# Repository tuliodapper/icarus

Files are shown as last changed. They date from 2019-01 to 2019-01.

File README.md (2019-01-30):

# icarus
This project consists of designing, building and testing a mobile robot. The system is a self-contained robot able to negotiate a maze in the shortest possible time. In the micromouse project rules, the maze is composed by 16x16 squares; the goal (2x2 square) is placed in the centre of the maze. Starting from a corner of the maze, the micromouse needs to complete the maze without any external help. For completing the maze, firstly, the micromouse needs to find the centre. After that, the robot needs to return to the start position and then execute the fast route to the centre. The work involves a huge number of skills that is included in a mobile robot, such as working with embedded programming, designing and building PCB boards, dealing with sensor components and solving mechanical issues.

## Folders

### doc
Contains report, presentation and video.

### software
Contains MATLAB code for the control panel interface, which aims to monitor sensor values and set robot parameters. Use MATLAB R2015a or later versions.

### firmware
Contains C code for the firmware of the mobile robot.

### hardware
Contains the board EAGLE files for the hardware of the mobile robot.

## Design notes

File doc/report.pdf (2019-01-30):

Bristol, 24 May 2015

UFMFKA-30-2 – GROUP FAB LAB FINAL GROUP REPORT

# Group Fab Lab

# Final Group Report

Authors:

Ícaro Almeida (14004456)

Leonardo Jurado (10023227)

Sanyog Chhetri (13021702)

Túlio Dapper e Silva (14004454)

## Contents

## Section 1

### Introduction

The micromouse project consists of designing, building and testing a mobile robot. The

system is a self-contained robot able to negotiate a maze in the shortest possible time. In the

micromouse project rules, the maze is composed by 16x16 squares; the goal (2x2 square) is

placed in the centre of the maze. Starting from a corner of the maze, the micromouse needs

to complete the maze without any external help. For completing the maze, firstly, the

micromouse needs to find the centre. After that, the robot needs to return to the start position

and then execute the fast route to the centre.

The work involves a huge number of skills that is included in a mobile robot. The group

needs to work with programming for embedded systems, design and build of PCB boards,

deal with sensor components and solve mechanical issues. This document includes a brief

explanation about how the software and hardware were built and how the group has been

distributed tasks; in addition, it also includes the problems encountered and most suitable

approaches.

### Conceptual Design

The micromouse was designed in a modular approach. As a consequence, boards

could be more easily tested, modified and hardware issues could be solved separately. In

addition, a sensor board for testing could be built before designing and building the other

boards, which enabled the use of the Firecracker as the initial testing platform. At the end, as

the system was modular and the group faced an unexpected problem with the final sensor

board, the testing sensor board was still being used.

Four different boards were designed and built: power supply board, main board

(containing the microcontrollers), sensor board and motor board. In order to separate the

boards inside the micromouse, mechanical spacers were used. In total, the micromouse

ended up with 3 floors. In the first floor, the micromouse has two boards: the sensor board and

the motor board. The sensor board was placed on front of the motors for taking readings. The

motor board was place in the back of the motors. The main board is located in the second

floor; the last floor is used for the supply board.

On the supply board, a linear low dropout regulator was used with an appropriate heat

sink; reverse-polarity protection diodes and appropriate capacitors (as on the datasheet) were

also used. Two buttons and four LEDs were also placed on this board.

In order to store the programs into the microcontrollers, the group opted to design an

external board that can be attached to the main board via an Ethernet cable. On the external

board, there are switches to toggle between PIC 1 and 2. In both PICs, the PGC and PGD

pins were exclusively used for the burning process, avoiding switches; therefore it was

necessary to use the alternative UART ports.

On the motor driver board, the IC L293DNE was used as it supports the current drained

by the motors and also has diodes built-in. The only protective components attached outside

were the decoupling capacitors recommended on the datasheet and a unidirectional TVS as

it is faster than the bidirectional ones. A TVS is basically a diode with a lower breakdown

voltage, so it was used in addition to the internal diodes to protect the circuit from over voltages

generated by the motor coils as a consequence of the back-EMF.

On the sensor board, transistors were used to switch each IR LED due to the high

current they drain, which is nearly a hundred milliamps each.

### Project Planning

The group is composed of four members. In order to execute the micromouse work,

different tasks were assigned for each member. As a consequence, each member was

responsible for searching, developing, presenting and documenting their own part of the

project. During these stages, the other members were completely willing to help. The division

of the tasks were made as shown in Figure 1.

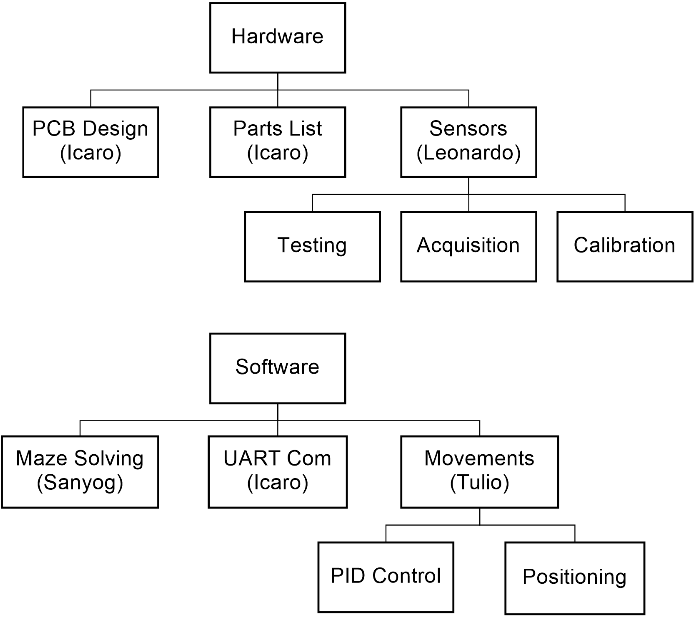
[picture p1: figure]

Figure 1: Division of the tasks between members.

As the project had deadlines to be respected, tasks should be executed within certain

period of time. In order to guarantee enough time for all tasks, a Gantt chart were built. The

first chart built is depicted in Figure 2. As can be seen in the figure, software structure (creating

headers with main constants and functions) and parts list should have be done by the end of

December. In addition, all the embedded programming should be finished by the middle of

January. The decision was based on having a long time for “Testing and Improvements”, which

should have two months of work. However, the work was not executed as planned.

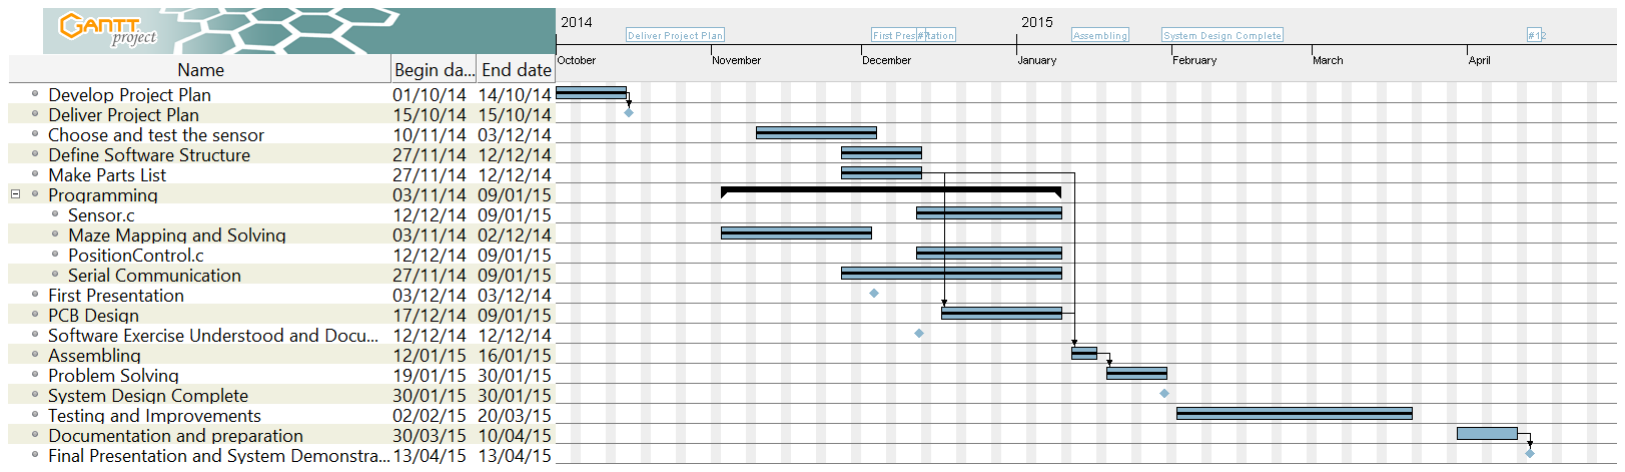
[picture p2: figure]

Figure 2: Gantt chart before executing the project.

At the end, the amount of time spent for each task is depicted in Figure 3. As can be

seen, some tasks took longer than expected. The main reason for those delays is that the

assigned duration for some tasks were not enough for the work load. The group were not

expecting to have problems that came from the lack of experience of the members. In addition,

most of the components were being frequently changed during the process. As a

consequence, the parts list was not completed in time; without the components, assembling

and testing were also being procrastinated. As a micromouse prototype was being used for

testing, the group was waiting as much as possible in order to design and build the final

version.

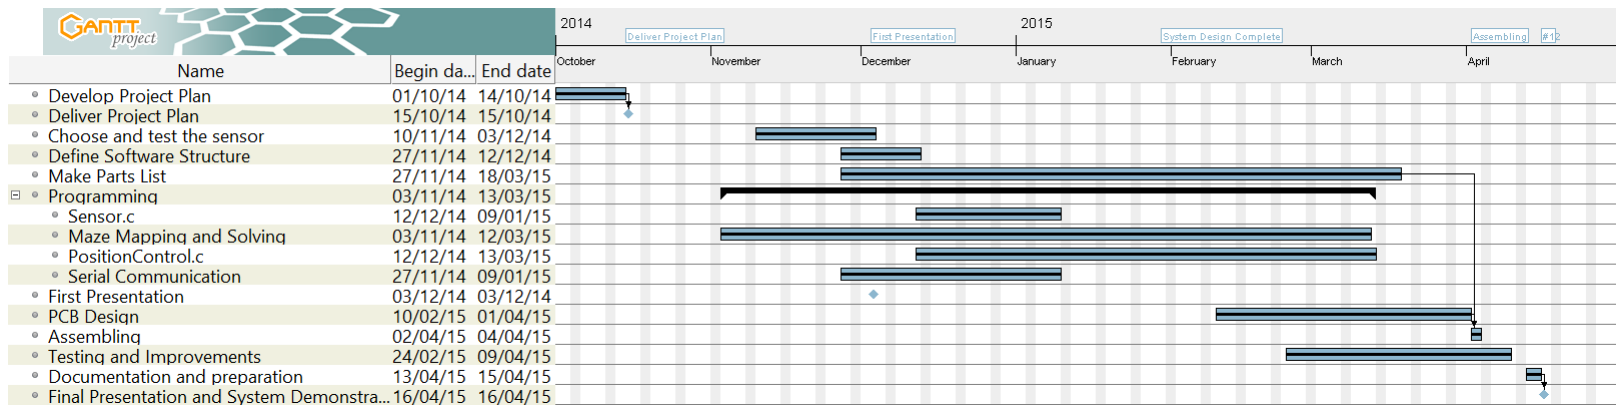
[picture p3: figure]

Figure 3: Gantt chart after executing the project.

### Controller Design

The software were designed in order to facilitate that each member could develop a

part separately. For that reason, meetings were needed in order to create headers and set up

how methods were interacting each other. The Figure 4 depicts, using UML class diagrams,

how main headers were designed and related each other.

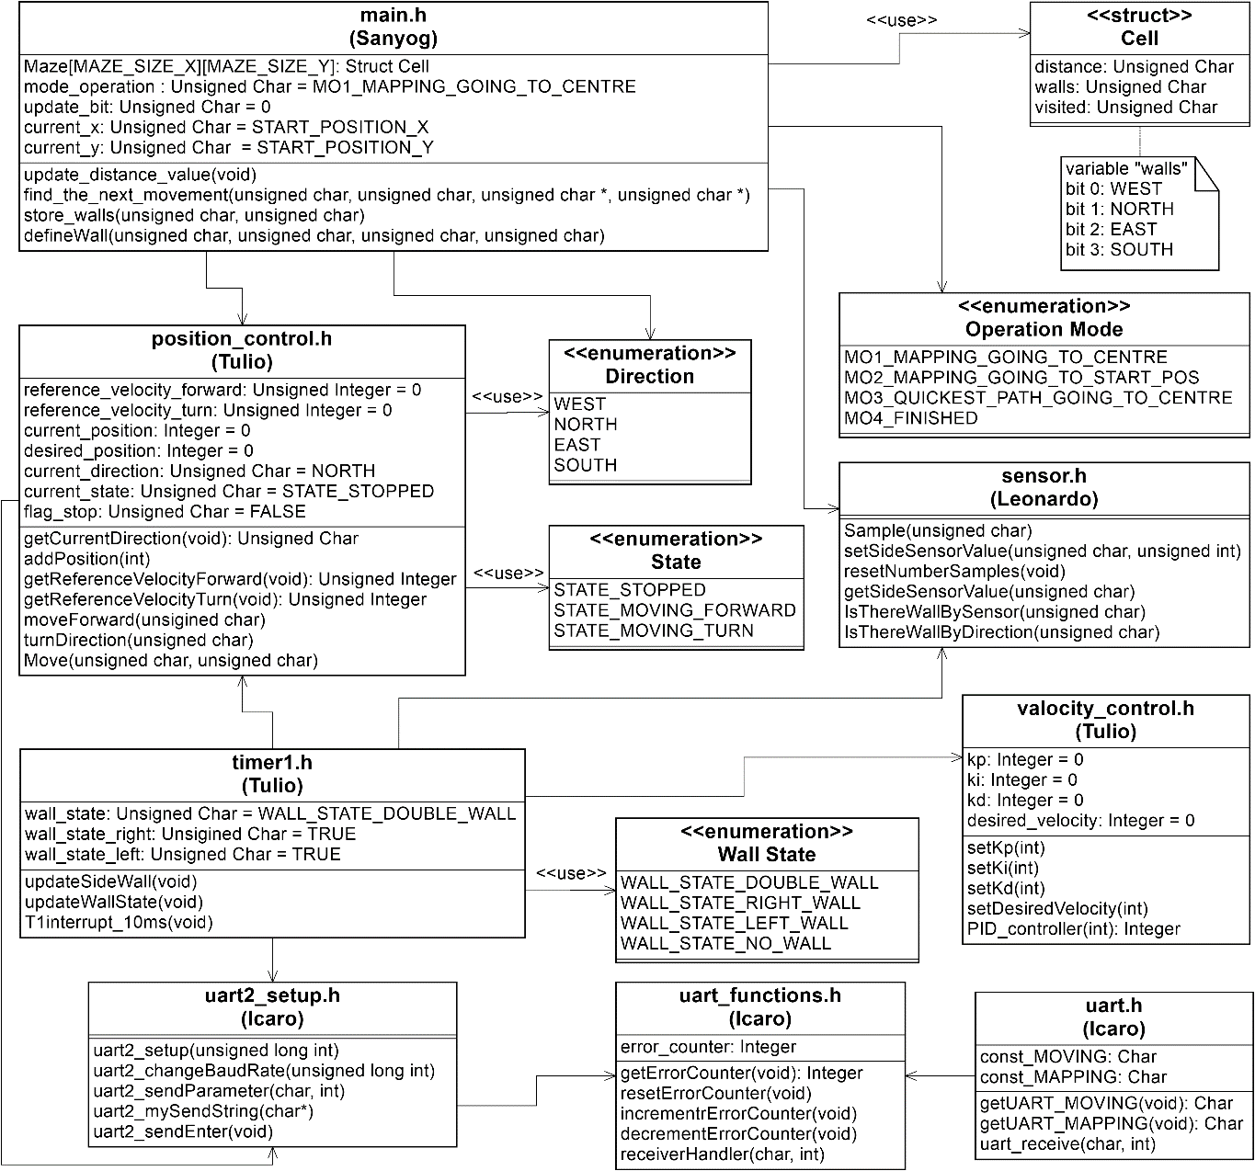
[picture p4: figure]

Figure 4: Software Design

The microcontroller dsPIC30F4011 supplied has only one quadrature encoder

interface (QEI). As the micromouse has two motors to be controlled, the system requires two

microcontrollers. One of them is the dsPIC30F4011, responsible for reading all sensors

values, controlling one motor, storing maze information and solving it. The second

microcontroller (dsPIC30F4012) is responsible for just controlling one of the motors; the desired velocity is sent by the first microcontroller using the UART communication. A different

PIC was used in order to avoid overpricing and oversizing of the system, as it has fewer pins.

The design of the software allowed both PICs to share the same libraries, such as

PWM, Timer, UART and PID Control. Setups and some other methods work for both PICs;

they do not have any change. If any improvement are made in a shared library, it will

automatically have effect on both PICs.

The Figure 5 shows the pin diagram of the microcontroller dsPIC30F4011 used as the

main PIC. The diagram was obtained from [4]. The Table 1 describes how the pins are being

used.

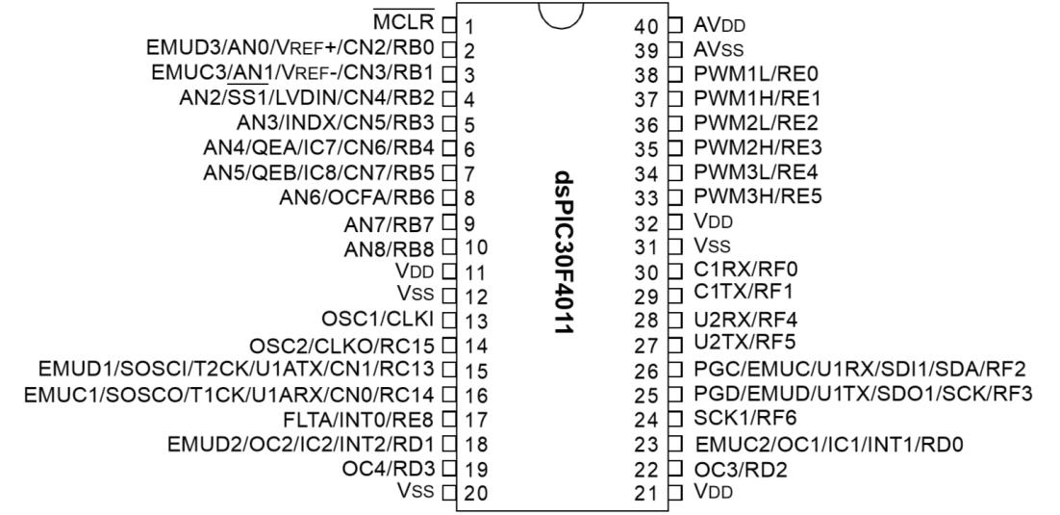
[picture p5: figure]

Figure 5: dsPIC30F4011 Pin Diagram

Table 1: Pin allocation for dsPIC30D4011

Port | Pin | Type | Function
| bit 0 | 2 | Digital Input | Button
| bit 1 | 3 | Analog Input | Sensor (Front Right)
| bit 2 | 4 | Analog Input | Sensor (Diagonal Right)
| bit 3 | 5 | Analog Input | Sensor (Right)
| bit 4 | 6 | Analog Input | Encoder A
| bit 5 | 7 | Analog Input | Encoder B
| bit 6 | 8 | Analog Input | Sensor (Left)
| bit 7 | 9 | Analog Input | Sensor (Diagonal Left)
| bit 8 | 10 | Analog Input | Sensor (Front Left)
| bit 13 | 15 | Digital Output | Bluetooth (Transmitter)
| bit 14 | 16 | Digital Input | Bluetooth (Receiver)

PORT B

PORT C

PORT D

bit 0 | 23 | Digital Output | Sensor Transistor (Right)
bit 1 | 18 | Digital Output | Sensor Transistor (Left)
bit 2 | 22 | Digital Output | Sensor Transistor (Front Right)
bit 3 | 19 | Digital Output | Sensor Transistor (Diagonal Left)
bit 0 | 38 | Digital Output | PWM
bit 1 | 37 | Digital Output | Motor Directional A
bit 2 | 36 | Digital Output | Motor Directional B
bit 3 | 35 | Digital Output | LED 1
bit 4 | 34 | Digital Output | LED 3
bit 8 | 17 | Digital Output | Sensor Transistor (Front Left)
bit 2 | 26 | Digital Input | PGC
bit 3 | 25 | Digital Output | PGD
bit 4 | 28 | Digital Input | UART2 Receiver
bit 5 | 27 | Digital Output | UART2 Transmitter
bit 6 | 24 | Digital Output | Sensor Transistor (Diagonal Right)

PORT E

PORT F

The Figure 6 shows the pin diagram of the microcontroller dsPIC30F4012. Basically,

this microcontroller was used only for receiving velocity information and make sure that the

second motor is spinning at the desired speed. The Table 2 describes how the pins are being

used by the program.

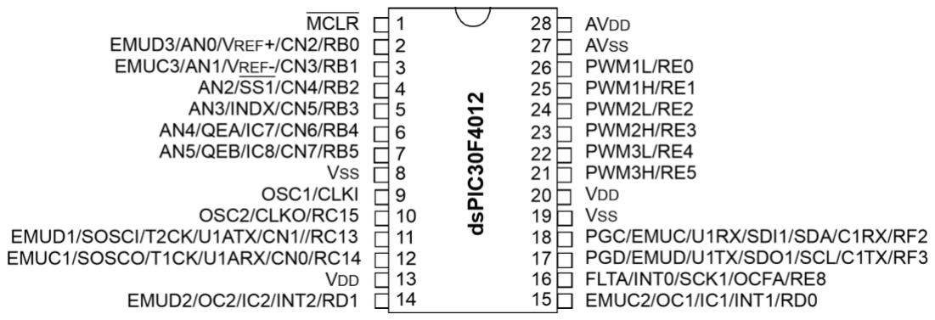
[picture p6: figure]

Figure 6: dsPIC30F4012 Pin Diagram

Table 2: Pin allocation for dsPIC30D4012

Port | Pin | Type | Function
| bit 4 | 6 | Analog Input | Encoder A
| bit 5 | 7 | Analog Input | Encoder B

PORT B

PORT C

bit 13 | 11 | Digital Output | Alt. UART1 Transmitter
bit 14 | 12 | Digital Input | Alt. UART1 Receiver

PORT D

bit 0 | 15 | Digital Output | LED 3
bit 1 | 18 | Digital Output | Button

PORT E

bit 0 | 26 | Digital Output | PWM
bit 1 | 25 | Digital Output | Motor Directional A
bit 2 | 24 | Digital Output | Motor Directional B
bit 8 | 16 | Digital Output | LED 4
bit 2 | 18 | Digital Input | PGC
bit 3 | 17 | Digital Output | PGD

PORT F

One of the main issues of the project is how to solve the maze. Some researches were

done and different methods were found such as A* Search, Using Stacks and Flood Fill

Algorithm. A* Search did not seem appropriated to be implemented, as it was apparently

difficult to be implemented. Using Stacks could not always find the shortest way to the centre.

Using that algorithm, there were a great amount of exceptions and if-else statements in order

to achieve the desired results. The best alternative found was the Flood Fill Algorithm.

Briefly, in the Flood Fill Algorithm, each cell contains a number which is the distance

value to the goal position; the distance value means how many cells are needed to reach the goal position. For every cell visited, the walls are stored and the distance values are updated.

In addition, the next cell to go is always the cell which contains the lowest distance value.

Using this method, after storing the wall information, the micromouse can pre-process the map

to attain better performance.

Using [2] as reference, the algorithm was written and debugged in MATLAB code. After

research, a library that allows a maze to be generated and drawn in MATLAB was found [3].

After modifying that library, the maze could be drawn informing the walls that the micromouse

already knows, the distance values and the current position of the micromouse. These visual

features obtained made it easier to simulate. The Figure 7Figure 8 shows the maze being

drawn during a simulation. The lines highlighted in black are the walls stored. The Hashtag

represents the robot.

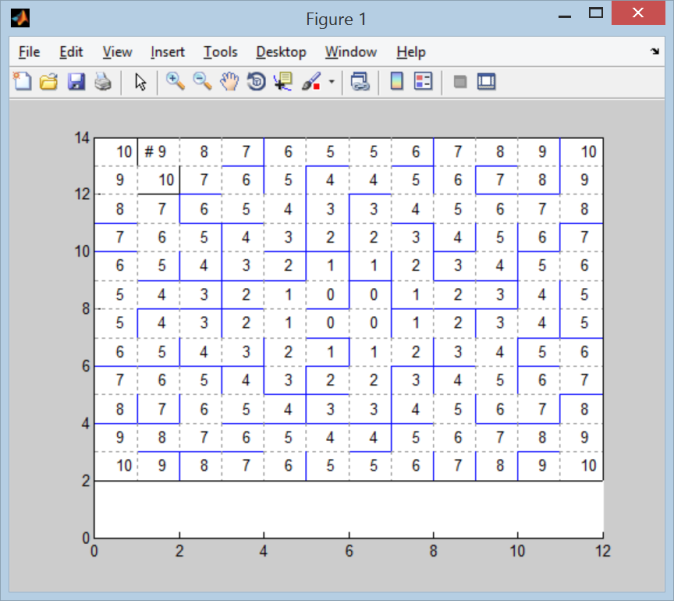
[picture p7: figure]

Figure 7: Flood Fill Algorithm being simulated using MATLAB.

The flow chart shown in Figure 8 was developed right after the algorithm properly

worked in simulation. In that way, the flow chart is an optimized version of the same code.

After that, the C code for the embedded programming was written based on the flow chart.

As can be seen in Figure 8, the logic starts with an initialization. At that stage, the

current position is updated to the starting position, the current direction is set to “NORTH” and

mode of operation is defined as 1. In addition, the cells, which contains the knowledge about

walls, distance to the goal and if the cell has been visited or not, are initialised. After that, the

outer walls are stored.

Defining the multi-dimensional array makes it easier to update the distance between

the mouse and the goal. Basically, this is achieved by giving the goal a value of zero and

incrementing the open neighbouring cell until it reaches the edges of the array.

Operation mode sets the state of the micromouse; the robot performs different task

depending on which operation it is on. The system has four mode operations. They are

described in Table 3.

Table 3: Operation Mode description

Operation Mode | Description
1 | Mapping the maze
2 | Going back to the starting position
3 | Quick run to the centre without searching
4 | Completed!

In the beginning of the while loop, the program checks whether the current operation

mode is 4; it terminates by being in an infinite loop which contains no task. Thus coming to a

hold.

During modes 1 and 2, the micromouse checks for walls, updates the distance values

and moves to the lowest neighbouring cell; this is done until the mouse reaches the goal. Then

the operation mode is incremented. The difference between them is that the goal position is

not the same. In operation mode 1, the goal position is the centre of the maze. On the other

hand, in mode 2, the goal position is the starting point. In addition, during operation mode 1,

after reaching the goal, the micromouse declares walls around the goal; due to there is only

one entrance.

In operation mode 3, the micromouse updates the distance values only once, before

starts moving. In order to determine the next movement, the cells which were not visited are

ignored; that makes that the micromouse does not get lost, being in cells that it has never

been. This also gives the mouse limited path and doesn't explore all the map. Before moving

to the next cell, the micromouse also calculates how many cells it needs to move in the same

direction. It allows the micromouse to reach a higher velocity depending on the number of

cells.

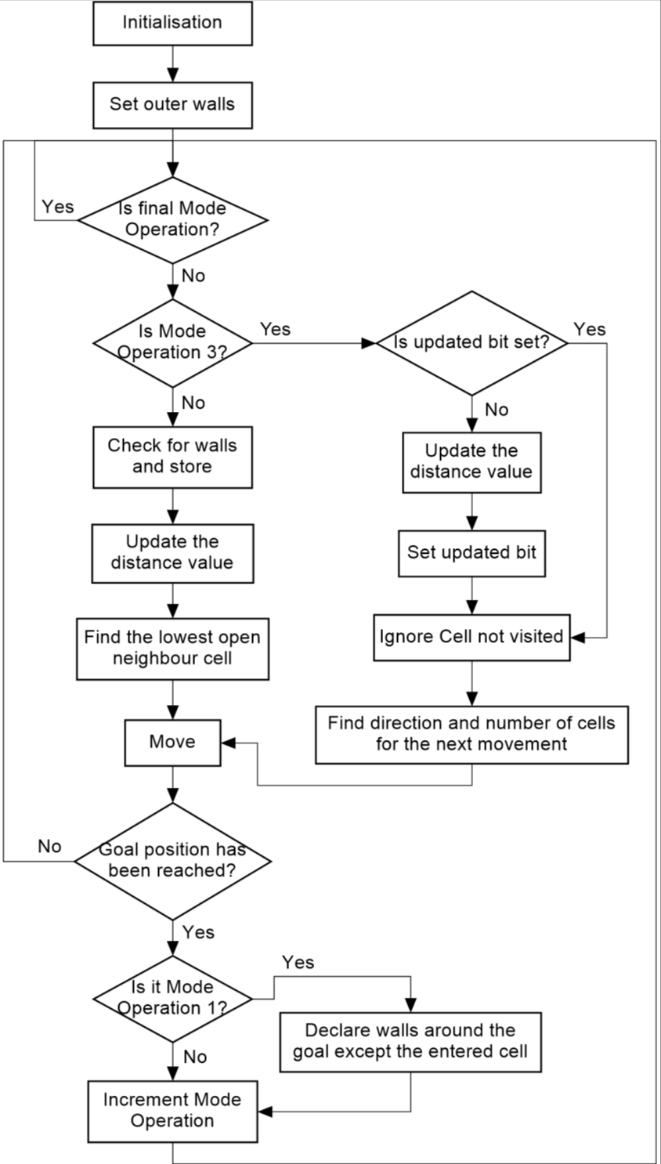
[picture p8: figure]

Figure 8: Flow Chart Diagram

## Section 2

### Sensor

The sensor information take an important role for the system. They are basically the

eyes of the micromouse. Having these data, the micromouse should be able to maintain in a

centre position in the cell, moving in a straight line and detect features of the maze, such as

walls and corners.

In a range of possible distance sensors, the group chose to work with infrared sensors.

The IR sensors are not accurate and the sunlight might cause interference; however, they are

cheaper than other options and, for the micromouse application, their performance is enough.

Some research were realized in order to find how their technical specification should

be. For the receiver, viewing angles are always wider than emitter [1]. Using the same

reference, angle of an IR receiver should be between 30 and 60 degrees. In addition, an IR

transmitter should emit light in a short range, under 10 degrees. Using those information, the

IR receiver used for the micromouse project is the “IR T-1 Photodiode 34° SFH229FA”; the

infrared transmitter is the “Infrared T-1¾ LED 850nm 6° SFH4550”.

The position of the sensors were decided based on research [1]. Six sensors were

placed in the front of the micromouse: one sensor looking to each side, one sensor looking to

each diagonal (approximately 45 degrees) and two sensors looking to the front. Initially, the

sensors placed in the diagonals did not have any assigned purpose. However, after testing

and programming the movements, they became fundamental for matching the virtual to the

real position.

After designing and building a PCB board for the sensors, they needed to be aligned.

The calibration was performed in two stages. Firstly, targets were drawn onto the walls in order

to align all the transmitters. Side sensors should be emitting with a same angle. The same for

diagonal sensors and front sensors. By using a camera the infrared could be seen and they

could be matched with the targets. After that stage, the IR receivers were adjusted. They

should be aligned in order to get the highest ADC values. The Figure 9 shows the infrared

lights captured by the camera during the sensors’ alignment.

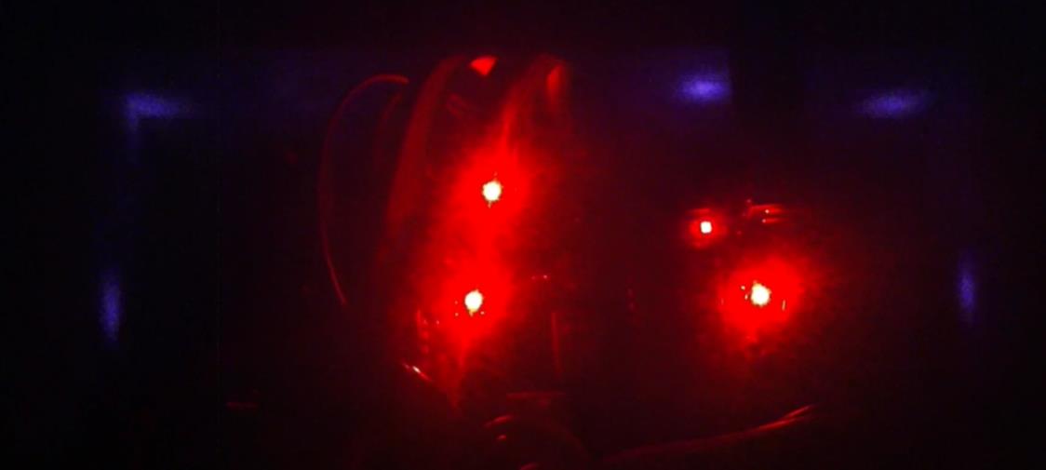
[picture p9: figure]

Figure 9: Aligning the sensors.

Finally, the resistors linked to the IR receivers needed to be selected. For that reason,

an “ADC Value x Distance” graph for four different resistance values was built. The highest

value in the graph is 810kΩ; as can be seen in Figure 10, the ADC Value reaches the

saturation when the object is close to the sensor. For that reason, 810kΩ was not used.

However, 706kΩ was chosen for the diagonal and front sensors. That value was chosen

because it responds in far distances. The 560kΩ was chosen for the side sensors. That

decision was made based on the sensibility in close distances. In addition, the side sensors

do not need to reach more than 10-12cm.

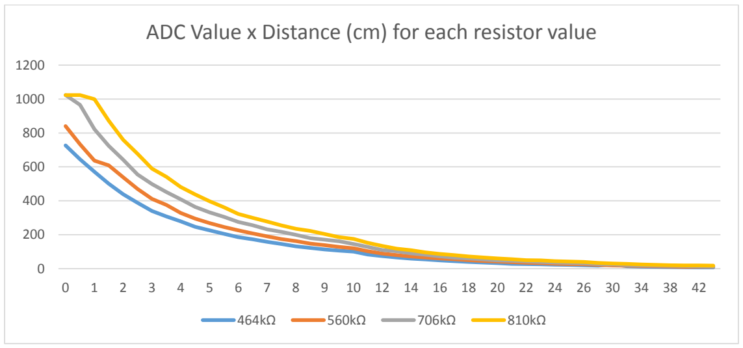
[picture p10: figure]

Figure 10: ADC Value x Distance for four different resistance values.

0 | 1 | 2 | 3 | 4 | 5 | 6 | 7 | 8 | 9 | 10 12 14 16 18 20 22 24 26 30 34 38 42

## ADC Value x Distance (cm) for each resistor value

### Control and Navigation

During the maze solving algorithm, a Cartesian coordinate system is used. Each

combination of x and y integer values represents a different cell. In order to assure the robot

is located where it should be, some procedures were taken; the virtual position needs to match

with the real position.

In order to perform the movements, the main logic takes the number of encoder pulses

into account. Firstly, some assumptions are made; the micromouse is moving in a straight line,

in the centre of the cell and both motors are spinning at a same velocity. In that case, a specific

number of pulses might indicates whether the robot has performed a turn or has moved a unit

of cell. However, after testing, as the robot was not moving in a perfect straight line, the number

of pulses could not perform the task for itself. Other logics were needed.

The first logic implemented is depicted in Figure 11. In this case, the micromouse

identifies a corner in the maze and then redefine the amount of pulses needed to be counted

in order to get to the centre of the next cell. Corners in both sides can be used to help in

positioning. In addition, the front sensors can also be used as reference. As shown in Figure

12, when the micromouse faces a wall in front, the ideal distance to the front walls can be

already known. The front walls should be also used to adjust the inclination of the micromouse,

but that technique was not implemented; it did not seem necessary in order to perform

properly.

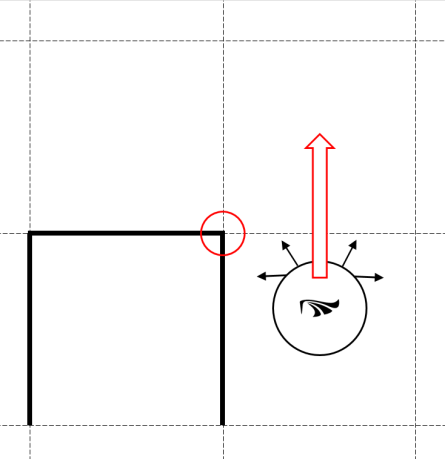
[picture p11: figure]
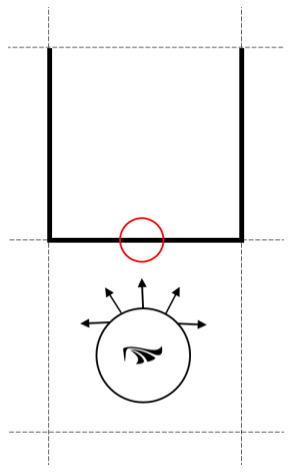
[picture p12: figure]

Figure 11: Position adjustment using corners. | Figure 12: Position adjustment using front sensors.

In order to move in a straight line, the distances from the robot to the walls in the sides

are used. Basically, the robot can face four different states: double walls (one wall each side),

only a wall at the right side, only a wall at the left side, or no walls in both sides.

The micromouse always starts in the state which there are two walls (one each side).

As can be seen in Figure 13, the sensors of both sides can be used in order to maintain the

robot centralized. The difference between both sensors can be add to the desired velocity of

both motors; then the robot will automatically correct your movement.

In the state which the there is only a wall at one side, the sensor data of the sensor

related to that side is used in order to maintain the robot in the centre of the cell. The difference

between the sensor data and the ideal distance is applied in the motors. As a consequence,

the micromouse will start using only one wall as reference.

In the last case, when the micromouse does not have any wall to use as reference, the

robot will basically move blinded. The system supposes that the robot is in central position;

then, the micromouse will not apply any correction speed.

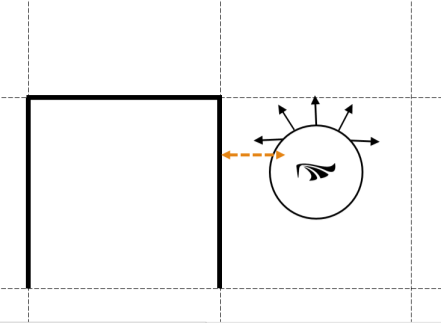
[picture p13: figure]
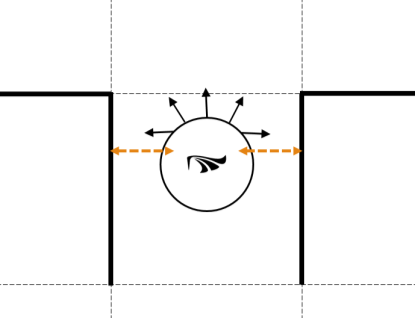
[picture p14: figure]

Figure 13: Maintain centralized in Double Wall state. Figure 14: Maintain centralized in Left Side Wall state.

After defining how the micromouse would move, all the constants need to be

determined. In order to find these values, a Bluetooth communication with the micromouse

was stabilised. Using that tool, the constants could be modified on real-time. In addition, an

interface could also show information about the system; as such as sensor values, speed and

duty cycle value.

In Figure 16 and Figure 17, the Bluetooth ICARUS Interface is connected to the

micromouse. The table shows the main constants. The column “Chr” indicates the character

used to send that value; as a consequence, the micromouse will be able to identify where that

value should be placed. The values are automatically sent to the micromouse when the user

modifies in the table. The button “Save” saves all those values in the computer. In order to

send all the current values to the micromouse, the button “Send all” was included. The button

“Reset” loads all saved values.

In the panel “Move”, the user can decide when the micromouse should move, pause

or stop. The “Stop” button resets all the maze and moving configuration. The “Pause” button

just freezes the micromouse movement. Marking the “Mapping” option, the user can view the

walls that the micromouse is storing, the position that the micromouse is virtually placed and

the distance value of each cell. In Figure 15, the mapping was performed in a real maze. The

micromouse is in operation mode 1; it is mapping the maze and searching for the centre.

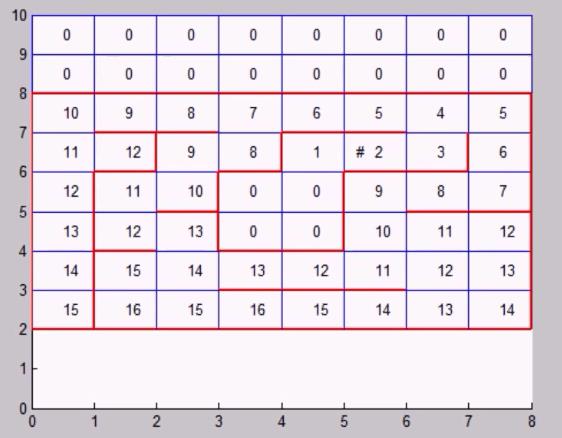
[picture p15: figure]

Figure 15: Visualizing the micromouse information on real-time.

In Figure 16, the Icarus Interface displays all the current sensor values. Using that tool,

ideal distances and thresholds values could be determined. In addition, the alignment of the

IR receiver should be performed. As the interface shows the sensor values in real-time, sensor

positions could be adjusted.

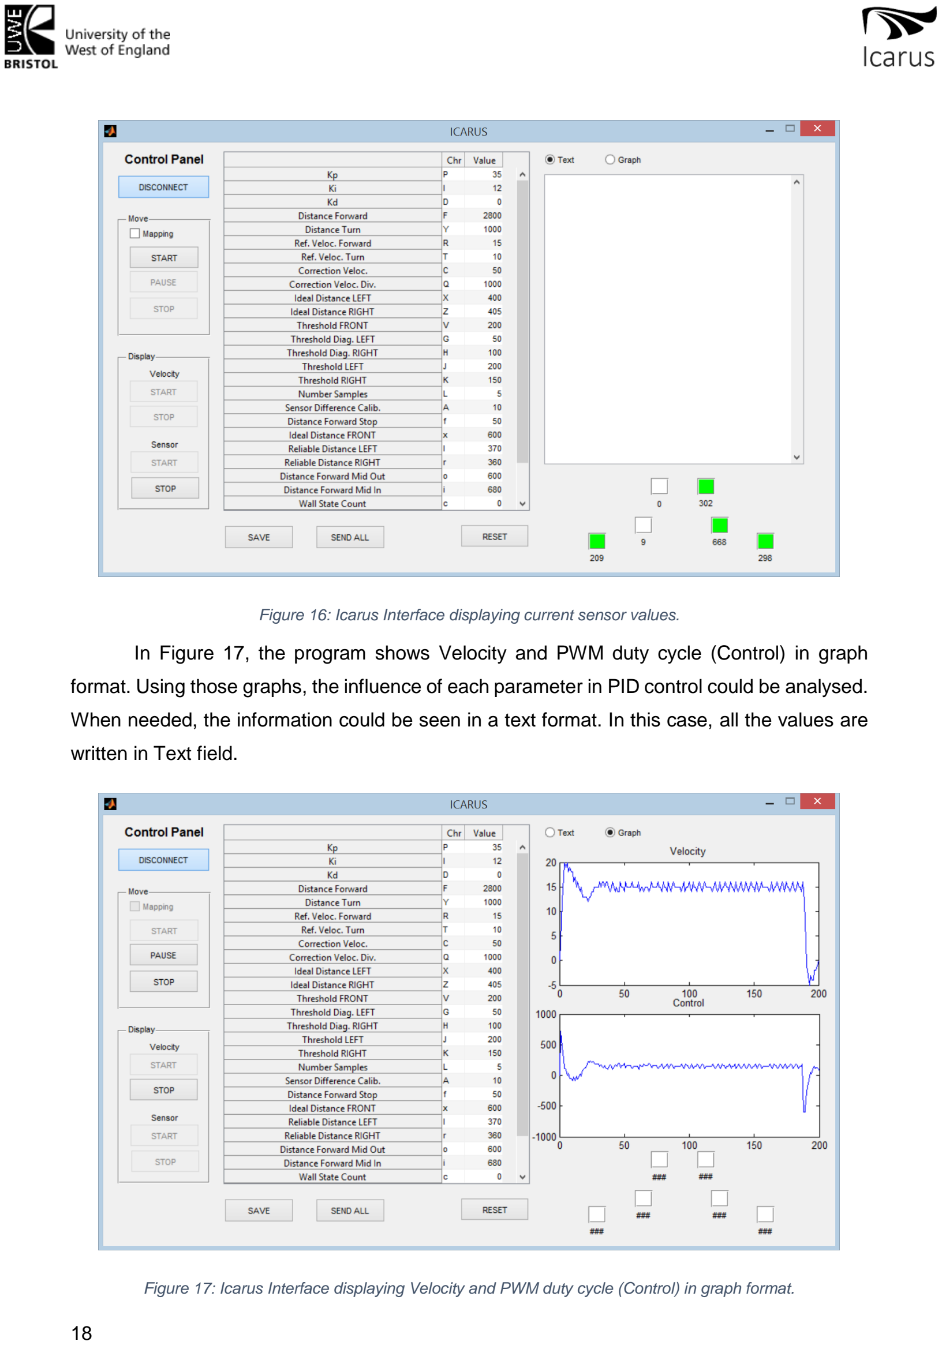
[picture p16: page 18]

Figure 16: Icarus Interface displaying current sensor values.

In Figure 17, the program shows Velocity and PWM duty cycle (Control) in graph

format. Using those graphs, the influence of each parameter in PID control could be analysed.

When needed, the information could be seen in a text format. In this case, all the values are

written in Text field.

Figure 17: Icarus Interface displaying Velocity and PWM duty cycle (Control) in graph format.

In order to tune the PID control, in the beginning, only the proportional parameter was

taken into account. As much the value was increased, the velocity started to be close to the

desired velocity. However, it never could reach the desired velocity. When the response

started having overshoot, the integrational parameter was then used. The integrational

parameter is able to nil the error in permanent state. The graph above shows the response of

the system when Kp = 36 and Ki = 12.

### Problems encountered

Since the beginning of the project, problems were faced. Initially, as the group did not

have motors and boards, the maze solving algorithm was a good start. A problem came up;

how to test and debug? The solution encountered was to use MATLAB in order to process the

algorithm, display the maze and the robot. Then, the group wanted to start working in a

prototype for testing. The idea was to use the Firecracker for testing. The prototype created is

depicted in Figure 18.

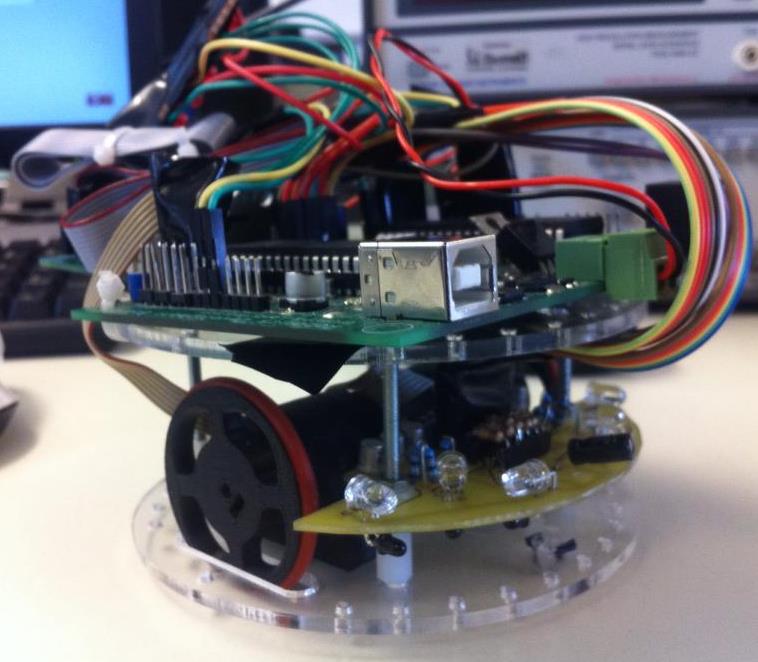
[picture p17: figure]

Figure 18: Prototype using Firecracker for testing.

During sensor testing, the group faced another unexpected problem: interferences

between different sensors and IR light was being transmitted through the board. In order to

solve the first problem, the code was changed in order to sample each sensor individually. In

addition, an isolation tape was placed between the transmitter and the receiver. In that way,

the IR light could not pass through the board.

After ordering the components, the group started mounting the final robot version

(Icarus). During the assembling, many problems were faced. During the PCB design, the size

of some connectors were not taken in account; as a consequence, during the mounting process, some of them needed to be cut. Others connectors needed to be removed therefore

wires were soldered directly onto the board.

In the prototype showed in Figure 18, a sensor board was placed in front of the motors

just below the Firecracker. Before building that prototype sensor board, two other boards were

built using strip-boards, however, they did not work properly. A PCB board was built. Initially,

this first PCB board was going to be used only for testing. However, as the group faced

problems with the tracks in the final sensor board, the testing board was used in the final

version (Icarus).

## Conclusion

The micromouse project involved working with different skills in the robot sector. The

group needed to work with sensor acquisition data, controlling motors, designing and building

PCBs. As usual, the group had to deal with problems, such as sensor inaccuracy, sensor

interferences, mechanical constrains and wrong components choices. All these facts were

important for learning and avoid same problems in further projects.

In terms of working in group, the project is an opportunity to improve that skill. As the

group had a great number of tasks to perform and deadlines were given, time management

needed to be taken into account since the beginning. For that, Gantt chart was designed and

tasks were divided between members. In order to check how each member was performing

individual tasks, internal presentations and individual deadlines were extremely essential.

An important learning is about documenting every step or decision taken. The group

has not written them down as desired. As a consequence, some thoughts and decisions were

lost; there were no way to remember the reason why some decisions had been made.

## Appendix

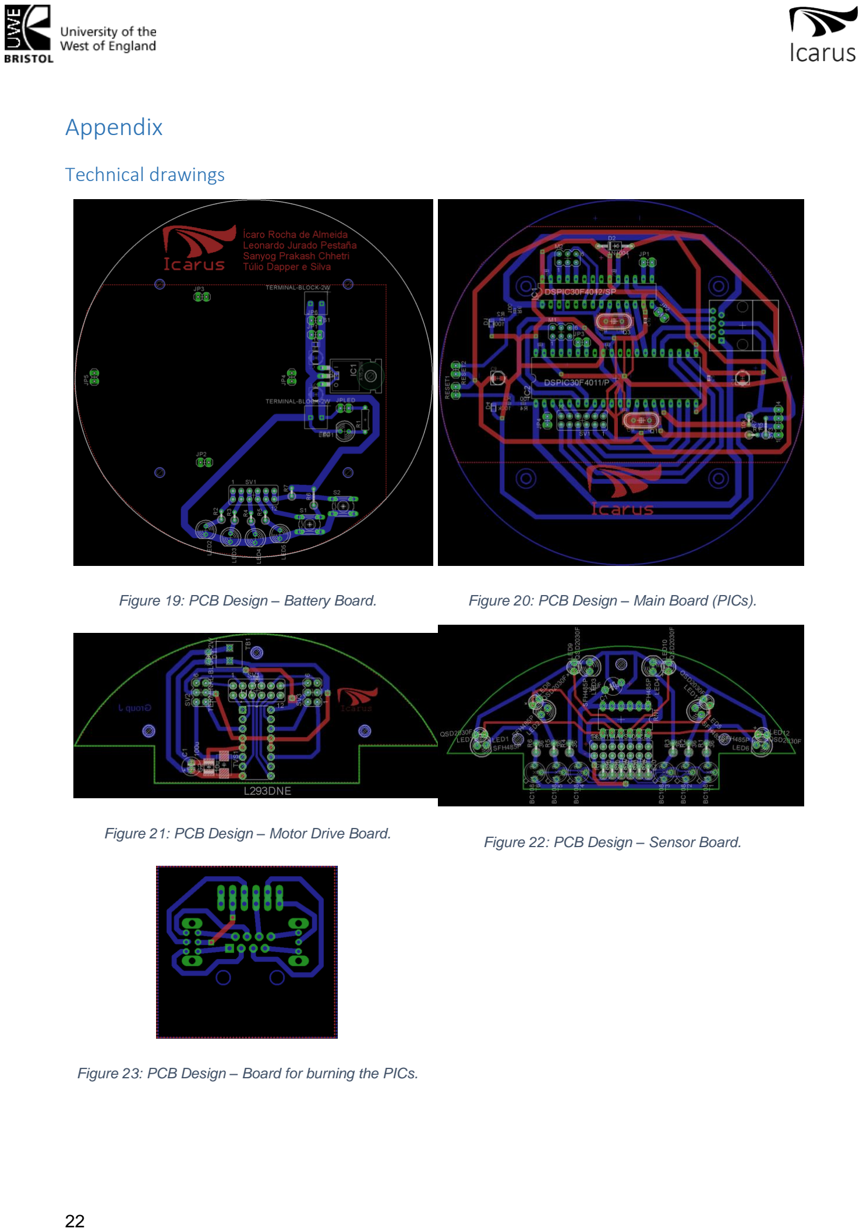
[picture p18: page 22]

### Technical drawings

Figure 19: PCB Design – Battery Board. | Figure 20: PCB Design – Main Board (PICs).
Figure 21: PCB Design – Motor Drive Board. | Figure 22: PCB Design – Sensor Board.

Figure 23: PCB Design – Board for burning the PICs.

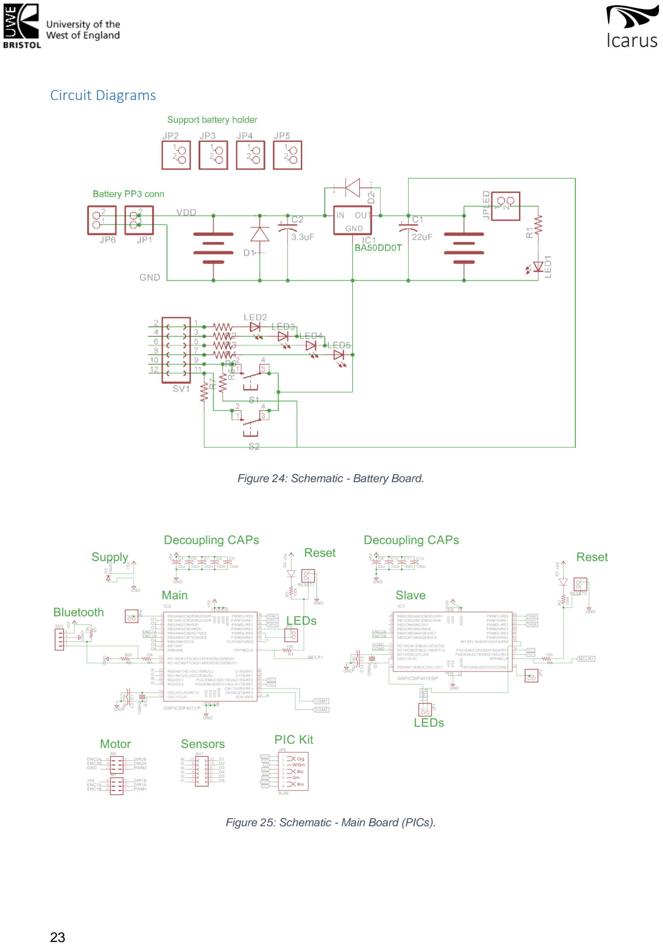
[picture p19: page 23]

### Circuit Diagrams

Figure 24: Schematic - Battery Board.

Figure 25: Schematic - Main Board (PICs).

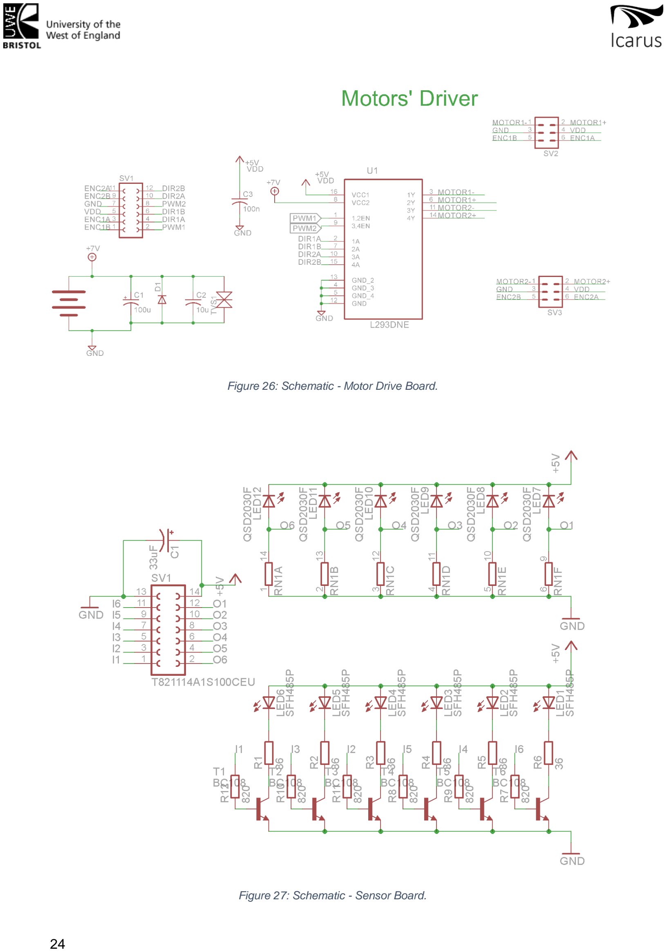
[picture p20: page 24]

Figure 26: Schematic - Motor Drive Board.

Figure 27: Schematic - Sensor Board.

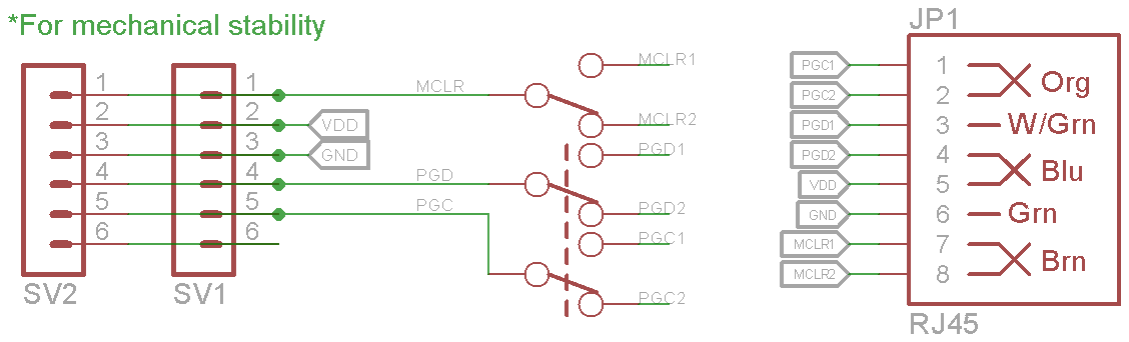
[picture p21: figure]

Figure 28: Schematic - Board for burning the PICs.

### Parts List and Costing

Qty | Order Code | Description of Goods | Unit Cost | Net Cost
3 | 1841939 | XTAL, 10.000MHZ, 18PF | 0.697 | £2.09
10 | 1539447 | ALU ELEC, 22UF, 6.3V, SMD | 0.16 | £1.60
3 | 1973360 | ALU ELEC, 3.3UF, 50V, SMD | 0.073 | £0.22
1 | 3829571 | BATTERY HOLDER, 6XAA | 3.74 | £3.74
4 | 1165527 | CAP, ALU ELEC, 22UF, 35V, RAD | 0.3 | £1.20
10 | 1759056 | CAP, MLCC, C0G/NP0, 18PF, 50V, 0603 | 0.0083 | £0.08
16 | 1759122 | CAP, MLCC, X7R, 100nF, 50V | 0.0083 | £0.13
2 | 1327750 | ceramic smd cap 10uF | 0.603 | £1.21
3 | 1611856 | CRYSTAL, 10MHZ, 18PF, HC49/S | 0.252 | £0.76
4 | 2335181 | diode 1n4004 | 0.0947 | £0.38
5 | 2341897 | DIODE, SCHOTTKY, 0.1A, 40V, 0603 | 0.0645 | £0.32
3 | 2341897 | DIODE, SCHOTTKY, 0.1A, 40V, 0603 | 0.0645 | £0.19
5 | 1017843 | DIODE, TVS, 9V, 600W, SMB | 0.409 | £2.05
10 | 1593452 | HEADER, 2 ROW, R/ANGLE, 12WAY | 0.149 | £1.49
10 | 1022238 | HEADER, 2ROW, 12WAY | 0.225 | £2.25
2 | 1513592 | HEADER, C-GRID III, VERT, 14WAY, 2ROW | 0.54 | £1.08
2 | 2215306 | HEADER, VERTICAL, 2.54MM, 12WAY | 0.513 | £1.03
3 | 2215307 | HEADER, VERTICAL, 2.54MM, 14WAY | 0.472 | £1.42
2 | 2215302 | HEADER, VERTICAL, 2.54MM, 6WAY | 0.368 | £0.74
1 | 4620902 | HEAT SINK, DIP, GLUE-ON, 46°C/W | 0.428 | £0.43
2 | 4302163 | HEAT SINK, FOR SMD, 123°C/W | 0.343 | £0.69
3 | 2215249 | IDC, S/RELIEF, 2.54MM, 14WAY | 0.519 | £1.56
1 | 1331561 | JACK, SMT, R/A, RJ45, 8P8C | 0.787 | £0.79
1 | 1524544 | JACK, THT, R/A, RJ45, 8P8C | 0.667 | £0.67
7 | 1573495 | LED, IR, 5MM, 850NM | 0.329 | £2.30
1 | 1524544 | MODULAR, JACK, THT, R/A, RJ45, 8P8C | 0.667 | £0.67
1 | 1668351 | RECEPTACLE, 2.54MM, DUAL, 12WAY | 1.33 | £1.33
2 | 1668358 | RECEPTACLE, 2.54MM, DUAL, 14WAY | 1.56 | £3.12
4 | 2335725 | red led | 0.0643 | £0.26
10 | 2330119 | RESISTOR, METAL , 36R, 0.6W, 1% | 0.0279 | £0.28
10 | 2331713 | RESISTOR, POWER, 100R, 0.2W, 5%, 0603 | 0.0062 | £0.06
5 | 2309107 | RESISTOR, THICK FILM, 100KOHM, 100MW, 1% | 0.002 | £0.01
2 | 2215248 | SOCKET, IDC, S/RELIEF, 2.54MM, 12WAY | 0.525 | £1.05
8 | 1466845 | SPACER, M3X12-NI | 0.32 | £2.56
6 | 1466796 | SPACER, M3X25-NI | 0.355 | £2.13
1 | 2435095 | SWITCH SLIDE DPDT | 0.42 | £0.42
1 | 2435104 | SWITCH SLIDE SPDT | 0.33 | £0.33
2 | 2396053 | SWITCH, TACTILE, 50MA, 12VDC, SMD | 0.173 | £0.35
2 | 3882615 | TERMINAL BLOCK, WIRE TO BRD, 2POS | 0.281 | £0.56
| | | Net Total: | £41.52
| | | VAT: | £8.30
| | Gross Total: | | £49.82

## References

[1] Green, Y. (2015). Lecture 5: Parts/design Choices [online]. Available from:

http://micromouseusa.com/?page_id=1342 [Accessed 12 February 2015].

[2] Harsh, V. Micromouse Project [online]. PostDoctoral, University of Southern California.

Available from: robotics.usc.edu/~harsh/docs/micromouse.pdf [Accessed 03 February 2015].

[3] | Kubica, | J. | (2003). | Maze | Toolbox | [online]. | Available | from:

http://www.cs.cmu.edu/~jkubica/code/matlabMaze.html [Accessed 05 November 2014].

[4] | Microchip | (2005) | dsPIC30F | Family | Overview | [online]. | Available | from:

http://ww1.microchip.com/downloads/en/devicedoc/70043F.pdf [Accessed 28 October 2014].

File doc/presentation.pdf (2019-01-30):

# Icarus

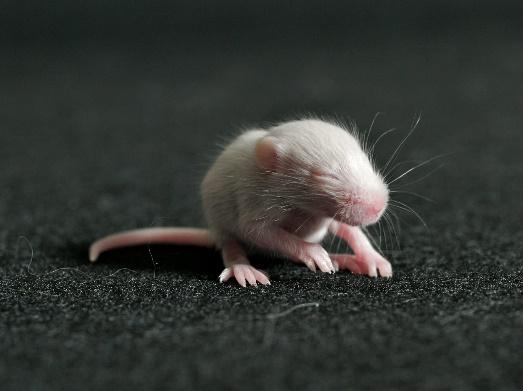
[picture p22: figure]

G ROUP J :
Í C A RO A LMEI DA

LEON A RDO J URA DO
SA N YOG C HHETRI
TÚLI O DA PPER

# Micromouse

# Topics:

Introduction
- Project description

Review
- Gantt Chart review

Progress
- Achievements
- Difficulties

Reflection
- Learnings
- How to improve the group work for a next project?

# Introduction: Project description

Design, build and test a mobile robot.
Micro-mouse competition.
Maze 16 x 16
Mice needs to
go to the centre
come back to start position fastest route to the centre Involves
programming embedded systems design electronic circuits and PCBs implement mapping algorithms Group work.

# Review: Gantt Chart review

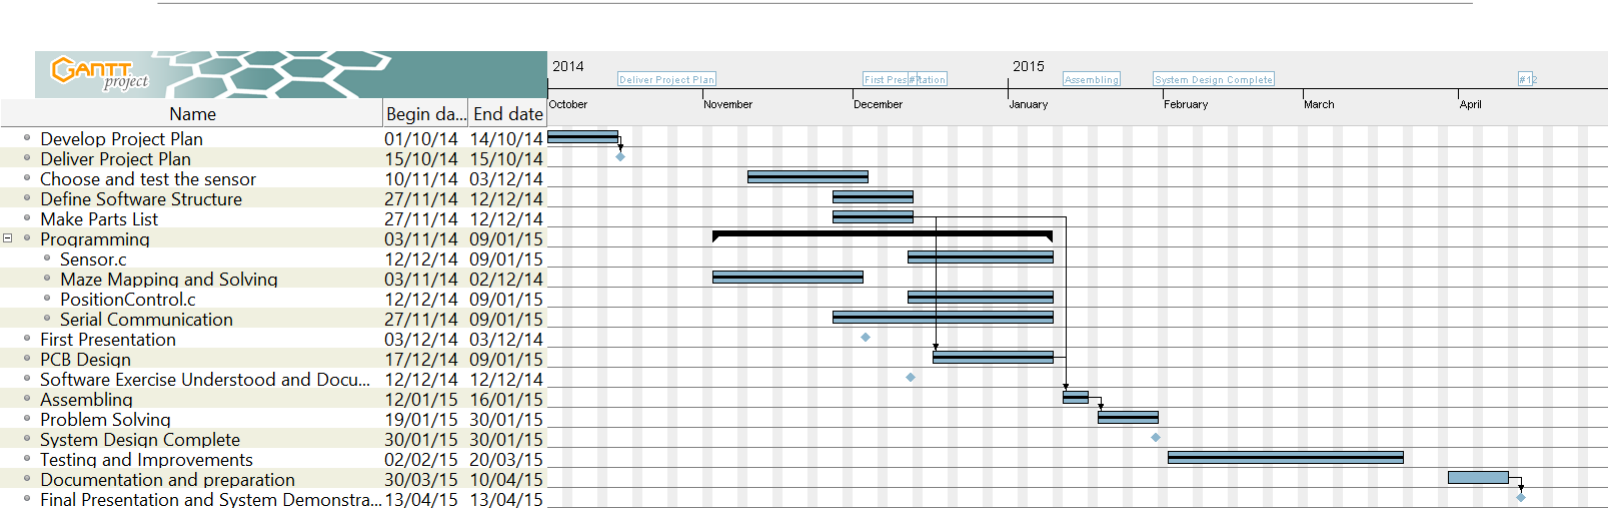
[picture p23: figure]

# Review: Gantt Chart review

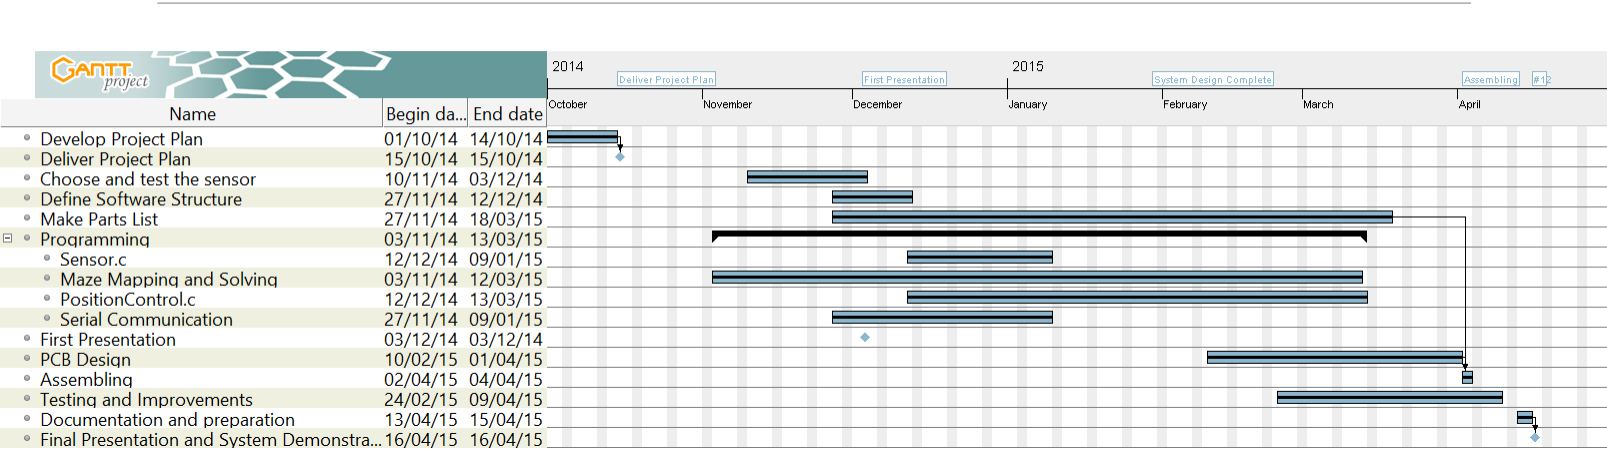
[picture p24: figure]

# Progress: Maze Solving


Which algorithm to use?
- A* Search
- Using Stacks
- Flood fill Algorithm
How it works?
- Each cell contains a number which is the distance value to the goal.
- The values are recalculated after each movement of the robot.
- The next step is always the cell which contains the lowest distance value.
Operation modes
- 1 - Mapping the maze
- 2 - Going back to the starting position
- 3 - Going through the quickest path without searching
- 4 - Completed!

# Progress: Maze Solving


How to simulate the algorithm?
- Using MATLAB.

# Progress: Sensors

Which sensors to use?
- Transmitter: viewing angle under 10 degrees.
- Receiver: viewing angles are always wider than emitter. Between 30-60 degrees.
- Source: http://micromouseusa.com/wp-content/uploads/2014/02/lecture-5-Parts_design-choicespart1.pptx


Where place the sensors?
- Two sensors
- Looking forward.
- Looking to each side.
- Looking to each diagonal.
Which resistance values to use?

# Progress: Sensors

◦ Front Sensors: 706k ◦ Diagonal Sensors: 706k ◦ Side Sensors: 560k

0 0,5 1 1,5 2 2,5 3 3,5 4 4,5 5 5,5 6 6,5 7 7,5 8 8,5 9 9,5 10 11 12 13 14 15 16 17 18 19 20 21 22 23 24 25 26 28 30 32 34 36 38 40 42 44

ADC Value x Distance (cm) for each resistor value

464k | 560k | 706k | 810k

# Progress: Sensors

How to solve interference problems?

Switch each IR at a different time
- Make light compensation possible
- Avoid reflection between the sensors
- At the end light compensation was not necessary

Put tape on the board to prevent light from passing through it

# Progress: Movements

How to determine that the mouse would have
- moved one cell?
- turned 90 degrees?

For each movement, count the number of encoder pulses needed

Can we trust this only? No!

Some additional method is needed!

# Progress: Movements


# Progress: Hardware

Bluetooth
- On-time connection
- Adjusting parameters
- Reading sensors/internal variables’ values
- MATLAB was the interface used for such

Modular approach to PCB design
- Power supply
- Control Board
- Sensor Board
- Motor Board


Used both 4011 and 4012
- Less pins, same configuration
- Avoid oversizing and overpricing of the system
External frequency


- Increased from 8MHz to 10MHz (Internal fcy from 64MHz to 80MHz) Use previously owned AA batteries


# Progress: Hardware

“Unexpected item in the designing area” Outer dimensions of some components were neglected
- Resulting in cutting connectors’ edges
Sensor board supply couldn`t go through the ribbon cable due to high current
- Exclusive supply was necessary
Sensor PCB prototype turned out to be the actual final board
Board for burning the PIC
- RJ45 cable only works in one direction
- Left the PGD and PGC connections exclusive for the PIC Kit
- Used the alternative UART1 pins instead


Took the challenge of using SMD components
- Solid state capacitor, 0603 resistors and diodes
- The diodes didn`t have exposed side connections

# Progress: Bluetooth


# Reflection

- Assign tasks according to each member’s interest and knowledge;
- Having regular meetings to update group progress;
- Set deadlines and presentations for individual tasks;
- Integration for the members of the group.

# Thank you! And… Enjoy the summer!


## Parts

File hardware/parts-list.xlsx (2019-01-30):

Order Code | Component PART No. | Package | via/pin | Description | Price (Unit) | Quantity | Total price
MICROCONTROLLER
1439598 | DSPIC30F4011-30I/P | PDIP | 40 | Microcontroller | 5.82 | 2 | 11.64
4285669 | 2227-40-06-05 | DIP | 40 | DIP 40 socket | 0.357 | 2 | 0.714
1703597 | XT49S-208M | Crystal | 2 | Crystal 8MHz (20pF) | 0.386 | 2 | 0.772
2332762 | 08055A200JAT2A | SMD 0805 | 2 | Ceramic smd cap 20pF | 0.0978 | 10 | 0.978
1536490 | 95501-2661 |  | 6 | RJ11 Jack | 0.609 | 2 | 1.218
2335181 | 1N4004-E3/54 |  | 2 | diode 1n4004 | 0.0947 | 6 | 0.5682
1125137 | 90075-0031 |  | 6 | RJ11 plug | 0.585 | 1 | 0.585
POWER SUPPLY |  |  |  |  |  |  | 0
1702629 | 2460 |  | 2 | 1xAA battery holder | 1.08 | 6 | 6.48
2342813 | BA05CC0FP-E2 | TO-252-3 | 3 | 5V regulator 300mV dropout | 0.394 | 2 | 0.788
4314001 | FK 244 08 D PAK |  |  | Heat sink for the above item | 0.664 | 1 | 0.664
8767246 | ECA1VAM470X | 5mm diam. | 2 | CAP, ALU ELEC, 47uF, 35V | 0.0942 | 3 | 0.2826
1759122 | MC0603B104K500CT | SMD0603 | 2 | CAP, MLCC, X7R, 100nF, 50V | 0.0083 | 10 | 0.083
2317545 | BC548BRL1G | TO-92-3 | 3 | TRANSISTOR, NPN, 30V, 100MA | 0.091 | 8 | 0.728
3882615 (http://uk.farnell.com/camdenboss/ctb3051-2bk/terminal-block-wire-to-brd-2pos/dp/3882615) | CTB3051/2BK (http://uk.farnell.com/camdenboss/ctb3051-2bk/terminal-block-wire-to-brd-2pos/dp/3882615) |  | 2 | TERMINAL BLOCK, WIRE TO BRD, 2POS (http://uk.farnell.com/camdenboss/ctb3051-2bk/terminal-block-wire-to-brd-2pos/dp/3882615) | 0.281 | 2 | 0.562
1593458 | 2212S-02SG-85 |  | 2 | RECEPTACLE, THT, VERTICAL, 2.54MM, 2WAY | 0.11 | 50 | 5.5
2335725 |  | 5mm diam. | 2 | red led | 0.0643 | 2 | 0.1286
2335726 |  | 5mm diam. | 2 | green led | 0.0643 | 2 | 0.1286
2335731 |  | 5mm diam. | 2 | yellow led | 0.0643 | 2 | 0.1286
MOTOR DRIVER |  |  |  |  |  |  | 0
1470423 | L293DNE | PDIP | 16 | Motor driver Bridge LDO | 2.76 | 1 | 2.76
1327750 | 1210ZC106KAT2A | SMD1210 | 2 | ceramic smd cap 10uF | 0.603 | 3 | 1.809
1827696 | SMBJ8.5CA | SMB | 2 | DIODE, TVS, 8.5V, 600W, BIDIR | 0.121 | 3 | 0.363
2215248 | T812112A101CEU | SOCKET IDC | 12 | SOCKET, IDC, S/RELIEF, 2.54MM, 12WAY | 0.525 | 2 | 1.05
2215306 | T821112A1S100CEU | HEADER IDC | 12 | HEADER, VERTICAL, 2.54MM, 12WAY | 0.513 | 3 | 1.539
1716261 (http://uk.farnell.com/rohm/bd6221f-e2/ic-h-bridge-driver-18v-1a-sop8/dp/1716261) | BD6221F-E2 (http://uk.farnell.com/rohm/bd6221f-e2/ic-h-bridge-driver-18v-1a-sop8/dp/1716261) | SOP8 | 8 | H BRIDGE DRIVER, 18V, 1A, SOP8 | 2.1 | 2 | 4.2
4302163 | ICK SMD A 5 SA |  |  | HEAT SINK, FOR SMD, 123°C/W | 0.343 | 2 | 0.686
MECHANICAL |  |  |  |  |  |  | 0
1466785 | 05.13.081 | M3 |  | SPACER, M3X8-VZK | 0.3 | 10 | 3
1466837 | 05.13.351 | M3 |  | SPACER, M3X35-VZK | 0.354 | 4 | 1.416
1419986 | M36 PRSTMCZ100- | M3 |  | SCREW, STEEL, BZP, 6MM, M3, PK100 | 1.59 | 0 | 0
1419447 (http://uk.farnell.com/duratool/m3-hfst-z100/nut-full-steel-bzp-m3-pk100/dp/1419447) | M3- HFST-Z100- (http://uk.farnell.com/duratool/m3-hfst-z100/nut-full-steel-bzp-m3-pk100/dp/1419447) | M3 |  | NUT, FULL, STEEL, BZP, M3, PK100 (http://uk.farnell.com/duratool/m3-hfst-z100/nut-full-steel-bzp-m3-pk100/dp/1419447) | 1.27 | 0 | 0
 |  |  |  |  |  |  | 0
 |  |  |  |  |  |  | 0
MECHANICAL |  |  |  |  |  |  | 0
1212738 | SFH485P | 5mm | 2 | IR EMITTER, 880NM, 5MM, RADIAL | 0.468 | 6 | 2.808
2453251 | QSD2030F | 5mm | 2 | PHOTODIODE, 880NM, 20DEG, 5MM | 0.58 | 6 | 3.48
 |  |  |  |  |  |  | 0
 |  |  |  |  |  |  | 0
 |  |  |  |  |  |  | 0
 |  |  |  |  |  |  | 48.7716

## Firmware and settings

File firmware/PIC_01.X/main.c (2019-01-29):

// PIC 01

#include <p30Fxxxx.h>
#include "main.h"
#include "adc.h"
#include "io.h"
#include "position_control.h"
#include "uart.h"
#include "sensor.h"
#include "timer1.h"
#include "bluetooth_setup.h"
#include "../pwm_setup.h"
#include "../timer1_setup.h"
#include "../uart1_setup.h"
#include "../uart2_setup.h"
#include "../uart_functions.h"
#include "../qei.h"
#include "../delay.h"
#include "../velocity_control.h"
#include <stdio.h>
#include <stdlib.h>
#include <string.h>

_FOSC(PRI & XT_PLL8 & CSW_FSCM_OFF);

_FWDT(WDT_OFF);

_FBORPOR(PBOR_OFF & MCLR_EN & PWRT_64 & PWMxL_ACT_HI & PWMxH_ACT_LO & RST_PWMPIN);

struct Cell {
    unsigned char distance; //indicates the distance to destination point
    unsigned char walls; //POSITION west=0 1=north 2=east 3=south
    unsigned char visited; //variable indicates has been in this cell or not
};

static struct Cell Maze[MAZE_SIZE_X][MAZE_SIZE_Y];

static unsigned char mode_operation;


void sendParameterInfo(int x, int y, int walls) {
    char str[15];
    sprintf(str, "%02d%02d%02d\r\n", x, y, walls);
    uart1_mySendString(str);
}

void sendINFO2PC(unsigned char current_x, unsigned char current_y, unsigned char walls) {
//    incrementErrorCounter();
//
//    while (getErrorCounter() > 0);
//
//    resetErrorCounter();

    sendParameterInfo(current_x, current_y, walls);

}

void defineWall(unsigned char x, unsigned char y, unsigned char direction, unsigned char wall) {
    if ((x >= 0) && (x < MAZE_SIZE_X) && (y >= 0) && (y < MAZE_SIZE_Y)) {
        if (wall) Maze[x][y].walls |= (1 << direction);
        else Maze[x][y].walls &= ~(1 << direction);
    }
}

void defineDuoWall(unsigned char x, unsigned char y, unsigned char direction, unsigned char wall) {

    unsigned char new_x, new_y;
    defineWall(x, y, direction, wall);
    newxy_from_xy(direction, 1, x, y, &new_x, &new_y);
    defineWall(new_x, new_y, invert_direction(direction), wall);
}

unsigned char getWall(unsigned char x, unsigned char y, unsigned char direction) {
    return (Maze[x][y].walls & (1 << direction));
}

void newxy_from_xy(unsigned char direction, unsigned char no_cells, unsigned char current_x, unsigned char current_y, unsigned char * new_x, unsigned char * new_y) {
    if (direction == NORTH) {
        *new_x = current_x;
        *new_y = current_y + no_cells;
    } else if (direction == EAST) {
        *new_x = current_x + no_cells;
        *new_y = current_y;
    } else if (direction == SOUTH) {
        *new_x = current_x;
        *new_y = current_y - no_cells;
    } else {
        *new_x = current_x - no_cells;
        *new_y = current_y;
    }
}

void update_distance_value(void) {

    unsigned char x;
    unsigned char y;

    unsigned char direction;
    unsigned char new_x;
    unsigned char new_y;
    unsigned char level;

    unsigned char ff_stack[MAZE_SIZE_Y * MAZE_SIZE_X][2];
    int ff_counter = -1;
    unsigned char wall_stack[MAZE_SIZE_Y * MAZE_SIZE_X][2];
    int wall_counter = -1;

    for (x = 0; x < MAZE_SIZE_X; x++)
        for (y = 0; y < MAZE_SIZE_Y; y++)
            Maze[x][y].distance = 255;

    level = 0;

    if ((mode_operation == MO1_MAPPING_GOING_TO_CENTRE) || (mode_operation == MO3_QUICKEST_PATH_GOING_TO_CENTRE)) {
        for (x = (MAZE_SIZE_X / 2) - 1; x < ((MAZE_SIZE_X / 2) + 1); x++)
            for (y = (MAZE_SIZE_Y / 2) - 1; y < ((MAZE_SIZE_Y / 2) + 1); y++) {
                ff_counter++;
                ff_stack[ff_counter][0] = x;
                ff_stack[ff_counter][1] = y;
            }// setting zeros to centre.
    } else {
        ff_counter = 0;
        ff_stack[ff_counter][0] = START_POSITION_X;
        ff_stack[ff_counter][1] = START_POSITION_Y;
    }

    //repeat untill ff stack is empty
    while (ff_counter > -1) {
        while (ff_counter > -1) {
            x = ff_stack[ff_counter][0];
            y = ff_stack[ff_counter][1];
            ff_counter--;
            if (Maze[x][y].distance == 255) {
                Maze[x][y].distance = level;
                //OPEN_NEIGHBOUR_FUNCTION
                for (direction = 0; direction < 4; direction++) {
                    if (getWall(x, y, direction) == FALSE) {
                        wall_counter++;
                        //new_x and new_y
                        newxy_from_xy(direction, 1, x, y, &new_x, &new_y);
                        wall_stack[wall_counter][0] = new_x;
                        wall_stack[wall_counter][1] = new_y;
                    }
                }
            }
        }

        // The array ff_stack is now empty

        if (wall_counter > -1) {
            level++;
            memcpy(ff_stack, wall_stack, sizeof (ff_stack));
            ff_counter = wall_counter;
            wall_counter = -1;
        }
    }
}

unsigned char direction_from_xy(unsigned char current_x, unsigned char current_y, unsigned char new_x, unsigned char new_y) {
    if ((new_x > current_x) && (new_y == current_y))
        return EAST;
    else if ((new_x < current_x) && (new_y == current_y))
        return WEST;
    else if ((new_x == current_x) && (new_y > current_y))
        return NORTH;
    else
        return SOUTH;

}

void find_open_neighbour_cell(unsigned char current_x, unsigned char current_y, unsigned char ignore_not_visited_cells, unsigned char * direction) {

    unsigned char stack_open_neighbour[4][2];
    int stack_open_neighbour_position = -1;

    unsigned char new_x, new_y;
    unsigned char i;

    for (i = 0; i < 4; i++) {
        if (getWall(current_x, current_y, i) == FALSE) {
            newxy_from_xy(i, 1, current_x, current_y, &new_x, &new_y);
            if ((Maze[new_x][new_y].visited == TRUE) || (ignore_not_visited_cells == FALSE)) {
                stack_open_neighbour_position++;
                //new_x and new_y
                stack_open_neighbour[stack_open_neighbour_position][0] = new_x;
                stack_open_neighbour[stack_open_neighbour_position][1] = new_y;
            }
        }
    }


    unsigned char position_lowest = 0;
    for (i = 1; i < (stack_open_neighbour_position + 1); i++)
        if (Maze[stack_open_neighbour[i][0]][stack_open_neighbour[i][1]].distance < Maze[stack_open_neighbour[position_lowest][0]][stack_open_neighbour[position_lowest][1]].distance)
            position_lowest = i;

    *direction = direction_from_xy(current_x, current_y, stack_open_neighbour[position_lowest][0], stack_open_neighbour[position_lowest][1]);
}

void find_the_next_movement(unsigned char current_x, unsigned char current_y, unsigned char * no_cells, unsigned char * direction) {
    unsigned char next_direction;
    *no_cells = 0;

    find_open_neighbour_cell(current_x, current_y, TRUE, direction);
    newxy_from_xy(*direction, 1, current_x, current_y, &current_x, &current_y);

    next_direction = *direction;

    while (*direction == next_direction) {
        (*no_cells)++;
        find_open_neighbour_cell(current_x, current_y, TRUE, &next_direction);
        newxy_from_xy(next_direction, 1, current_x, current_y, &current_x, &current_y);
    }

}

unsigned char invert_direction(unsigned char direction) {
    if (direction == NORTH)
        return (SOUTH);
    else if (direction == SOUTH)
        return (NORTH);
    else if (direction == WEST)
        return (EAST);
    else
        return (WEST);
}

void store_walls(unsigned char current_x, unsigned char current_y) {
    FRONT_LEFT_SENSOR_Latch = 1;
    Sample(FRONT_LEFT_SENSOR);
    FRONT_LEFT_SENSOR_Latch = 0;

    FRONT_RIGHT_SENSOR_Latch = 1;
    Sample(FRONT_RIGHT_SENSOR);
    FRONT_RIGHT_SENSOR_Latch = 0;

    LEFT_SENSOR_Latch = 1;
    Sample(LEFT_SENSOR);
    LEFT_SENSOR_Latch = 0;

    RIGHT_SENSOR_Latch = 1;
    Sample(RIGHT_SENSOR);
    RIGHT_SENSOR_Latch = 0;

    defineDuoWall(current_x, current_y, getCurrentDirection(), IsThereWallBySensor(FRONT_LEFT_SENSOR));
    defineDuoWall(current_x, current_y, NextDirection(getCurrentDirection(), LEFT), IsThereWallBySensor(LEFT_SENSOR));
    defineDuoWall(current_x, current_y, NextDirection(getCurrentDirection(), RIGHT), IsThereWallBySensor(RIGHT_SENSOR));
}

void sendParameterToPIC02(char c, int value) {
    uart2_sendParameter(c, value);
    incrementErrorCounter();
    myDelay(500);
    while (getErrorCounter() > 0) {
        resetErrorCounter();
        uart2_sendParameter(c, value);
        incrementErrorCounter();
        myDelay(500);
    }
}

void ResetLocation(unsigned char * current_x, unsigned char * current_y) {

    *current_x = START_POSITION_X;

    *current_y = START_POSITION_Y;

    ChangeDirection(NORTH);
    
}

void Reset(unsigned char * current_x, unsigned char * current_y, unsigned char * update_bit) {

    unsigned char x; //center is the mod op 1st and 3rd goal
    unsigned char y;
    unsigned char i;

    ResetLocation(current_x, current_y);

    *update_bit = 0;

    mode_operation = MO1_MAPPING_GOING_TO_CENTRE;

    for (x = 0; x < MAZE_SIZE_X; x++)
        for (y = 0; y < MAZE_SIZE_Y; y++) {
            Maze[x][y].walls = 0; //indicates the distance to destination point
            Maze[x][y].distance = 0; //indicates the distance to destination point
            Maze[x][y].visited = 0; //variable indicates has been in this cell or not
        }

    /* ##### setting outer walls ##### */
    for (i = 0; i < MAZE_SIZE_X; i++) {
        defineWall(i, 0, SOUTH, TRUE); // wall
        defineWall(i, MAZE_SIZE_Y - 1, NORTH, TRUE); //east wall
    }
    for (i = 0; i < MAZE_SIZE_Y; i++) {
        defineWall(0, i, WEST, TRUE); //west wall
        defineWall(MAZE_SIZE_X - 1, i, EAST, TRUE); //south wall
    }
    /* ##### end of setting wall ##### */

   ResetParameters();

   if (getUART_MAPPING()) sendINFO2PC(99, 99, 0);

}

int main(void) {

    unsigned char update_bit = 0;

    unsigned char current_x = START_POSITION_X;
    unsigned char current_y = START_POSITION_Y;

    unsigned char centerx; //center is the mod op 1st and 3rd goal
    unsigned char centery;

    unsigned char no_cells;

    unsigned char direction;

    unsigned char i;

    io_setup();

    if (CONFIGURE_BLUETOOTH) {
        uart1_setup(BAUDRATE_BLUETOOTH_CONFIGURATION_MODE);
        bluetooth_setup();
    }

    uart1_setup(BAUDRATE_BLUETOOTH);
    uart2_setup(BAUDRATE_PIC);
    
    setKp(CONTROL_KP);
    sendParameterToPIC02('P', CONTROL_KP);
    setKi(CONTROL_KI);
    sendParameterToPIC02('I', CONTROL_KI);
    setKd(CONTROL_KD);
    sendParameterToPIC02('D', CONTROL_KD);

    pwm_setup();

    qei_setup();

    timer1_setup();

    adc_setup();

    sensor_setup();

    Reset(&current_x, &current_y, &update_bit);

        while (1) {

            if (getUART_MOVING() == 2) { // STOP
                Reset(&current_x, &current_y, &update_bit);
                setUART_MOVING(0);
            }

            if (getUART_MOVING() == 1) { // MOVE

                /* ##### is this Final mode operation? ##### */
                if (mode_operation != MO4_FINISHED) {

                    /* ##### is this mode operation 3? ##### */
                    if (mode_operation == MO3_QUICKEST_PATH_GOING_TO_CENTRE) {
                        //check update bit set
                        if (update_bit == 0) {
                            //update the distance value
                            update_distance_value();
                            //set update
                            update_bit = 1;
                        }

                        //ignore cell not visited
                        //find direction and number of cells for next movement
                        find_the_next_movement(current_x, current_y, &no_cells, &direction);

                    } else {
                        Maze[current_x][current_y].visited = 1;
                        //check for wall
                        store_walls(current_x, current_y);
                        //updating distance value
                        update_distance_value();
                        //Find the open neighbour cell with the lowest distance value
                        no_cells = 1;
                        find_open_neighbour_cell(current_x, current_y, FALSE, &direction);

                    }

                    if (getUART_MAPPING()) sendINFO2PC(current_x, current_y, Maze[current_x][current_y].walls);

                    Move(direction, no_cells, (mode_operation == MO3_QUICKEST_PATH_GOING_TO_CENTRE));

                    newxy_from_xy(direction, no_cells, current_x, current_y, &current_x, &current_y);

                    //is it goal position, is it mode operation1 yes? declare walls on goal
                    if (Maze[current_x][current_y].distance == 0) {

                        if (mode_operation == MO1_MAPPING_GOING_TO_CENTRE) {
                            for (centerx = (MAZE_SIZE_X / 2) - 1; centerx < ((MAZE_SIZE_X / 2) + 1); centerx++)
                                for (centery = (MAZE_SIZE_Y / 2) - 1; centery < ((MAZE_SIZE_Y / 2) + 1); centery++)
                                    for (i = 0; i < 4; i++)
                                        defineDuoWall(centerx, centery, i, TRUE);
                            defineDuoWall(current_x, current_y, invert_direction(direction), FALSE);
                        }
                        mode_operation++;
                    }
                } else {
                    if (getUART_MAPPING()) sendINFO2PC(current_x, current_y, Maze[current_x][current_y].walls);
                    // Celebrating
                    LED1Latch = 0;
                    LED2Latch = 0;
                    for (i = 0; i < 3; i++){
                        LED1Latch = 1;
                        myDelay(CELEBRATION_TIME_INTERVAL);
                        LED1Latch = 0;
                        myDelay(CELEBRATION_TIME_INTERVAL);
                        LED2Latch = 1;
                        myDelay(CELEBRATION_TIME_INTERVAL);
                        LED2Latch = 0;
                        myDelay(CELEBRATION_TIME_INTERVAL);
                    }
                    for (i = 0; i < 3; i++){
                        LED1Latch = 0;
                        LED2Latch = 0;
                        myDelay(CELEBRATION_TIME_INTERVAL);
                        LED1Latch = 1;
                        LED2Latch = 1;
                        myDelay(CELEBRATION_TIME_INTERVAL);
                    }
                    ResetLocation(&current_x, &current_y);
                    mode_operation = MO3_QUICKEST_PATH_GOING_TO_CENTRE;
                    setUART_MOVING(0);
                    if (getUART_MAPPING()) sendINFO2PC(98, 98, 0);
                }
            }

            if (getUART_MOVING() == 0) { // STOP

                // Delay aiming to have 1ms between samples.
                myDelay(1);

                // Verify how many samples the button is (un)pressed and the current value can be updated.
                read_buttons();

                // If the current value and the old value are in this configuration, so, act.
                if ((get_old_value_s3() == 1) && (get_current_value_s3() == 0))
                {
                    // Invert the output.
                    setUART_MOVING(2);
                }

                // Makes the old value equal to the current value
                reset_buttons();
            }

        }


    return 0;
}

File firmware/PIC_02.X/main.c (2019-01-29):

// PIC 02

#include <p30Fxxxx.h>
#include "main.h"
#include "timer1.h"
#include "io.h"
#include "../pwm_setup.h"
#include "uart.h"
#include "../uart_functions.h"
#include "../uart1_setup.h"
#include "../velocity_control.h"
#include "../qei.h"

_FOSC(PRI  &  XT_PLL8 & CSW_FSCM_OFF  ); 

_FWDT(WDT_OFF); 
 
_FBORPOR( PBOR_OFF & MCLR_EN & PWRT_64 & PWMxL_ACT_HI &  PWMxH_ACT_LO & RST_PWMPIN);

void myDelay(unsigned int inTimeMiliSeconds)
{
    unsigned int i, j;

    for (i=0;i<inTimeMiliSeconds;i++)
        for (j=0;j<1998;j++);

}

int main(void)
{
    int button = 0;

    io_setup();

    uart1_setup(BAUDRATE_PIC);

    pwm_setup();

    qei_setup();
    
    timer1_setup();

    DIRALatch = 1;
    DIRBLatch = 0;
    
    LED3Latch = 1;

    while(1)
    {
        // Delay aiming to have 1ms between samples.
        myDelay(1);

        // Verify how many samples the button is (un)pressed and the current value can be updated.
        read_buttons();

        // If the current value and the old value are in this configuration, so, act.
        if ((get_old_value_s3() == 1) && (get_current_value_s3() == 0))
        {
            if (button == 0) button = 1; else button = 0;
            // Invert the output.
            uart1_sendParameter('B', button);
        }

        // Makes the old value equal to the current value
        reset_buttons();

    };

        
    return 0;
}

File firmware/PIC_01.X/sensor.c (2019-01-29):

#include <p30Fxxxx.h>
#include "sensor.h"
#include "position_control.h"
#include "adc.h"
#include "io.h"

struct sensor {
    unsigned int channel;
    unsigned int threshold;
    unsigned int value;
};

struct side_sensor {
    unsigned char number_samples;
    unsigned int values[NUMBER_SAMPLES];
};

struct sensor array_sensor[6];

struct side_sensor array_side_sensor[2];

// START OF DELETING
static unsigned int const_IDEAL_DISTANCE_FRONT = IDEAL_DISTANCE_FRONT;
static unsigned int const_IDEAL_DISTANCE_LEFT = IDEAL_DISTANCE_LEFT;
static unsigned int const_IDEAL_DISTANCE_RIGHT = IDEAL_DISTANCE_RIGHT;
static unsigned int const_RELIABLE_DISTANCE_LEFT = RELIABLE_DISTANCE_LEFT;
static unsigned int const_RELIABLE_DISTANCE_RIGHT = RELIABLE_DISTANCE_RIGHT;
static unsigned int const_RELIABLE_DISTANCE_LEFT_IN = RELIABLE_DISTANCE_LEFT_IN;
static unsigned int const_RELIABLE_DISTANCE_RIGHT_IN = RELIABLE_DISTANCE_RIGHT_IN;
static unsigned int const_NUMBER_SAMPLES = NUMBER_SAMPLES;

void setRELIABLE_DISTANCE_LEFT(unsigned int value){
    const_RELIABLE_DISTANCE_LEFT = value;
}
unsigned int getRELIABLE_DISTANCE_LEFT(void){
    return const_RELIABLE_DISTANCE_LEFT;
}
void setRELIABLE_DISTANCE_RIGHT(unsigned int value){
    const_RELIABLE_DISTANCE_RIGHT = value;
}
unsigned int getRELIABLE_DISTANCE_RIGHT(void){
    return const_RELIABLE_DISTANCE_RIGHT;
}
void setRELIABLE_DISTANCE_LEFT_IN(unsigned int value){
    const_RELIABLE_DISTANCE_LEFT_IN = value;
}
unsigned int getRELIABLE_DISTANCE_LEFT_IN(void){
    return const_RELIABLE_DISTANCE_LEFT_IN;
}
void setRELIABLE_DISTANCE_RIGHT_IN(unsigned int value){
    const_RELIABLE_DISTANCE_RIGHT_IN = value;
}
unsigned int getRELIABLE_DISTANCE_RIGHT_IN(void){
    return const_RELIABLE_DISTANCE_RIGHT_IN;
}
void setIDEAL_DISTANCE_FRONT(unsigned int value){
    const_IDEAL_DISTANCE_FRONT = value;
}
unsigned int getIDEAL_DISTANCE_FRONT(void){
    return const_IDEAL_DISTANCE_FRONT;
}
void setIDEAL_DISTANCE_LEFT(unsigned int value){
    const_IDEAL_DISTANCE_LEFT = value;
}
unsigned int getIDEAL_DISTANCE_LEFT(void){
    return const_IDEAL_DISTANCE_LEFT;
}
void setIDEAL_DISTANCE_RIGHT(unsigned int value){
    const_IDEAL_DISTANCE_RIGHT = value;
}
unsigned int getIDEAL_DISTANCE_RIGHT(void){
    return const_IDEAL_DISTANCE_RIGHT;
}
void setTHRESHOLD_FRONT(unsigned int value){
    array_sensor[FRONT_RIGHT_SENSOR].threshold = value;
    array_sensor[FRONT_LEFT_SENSOR].threshold = value;
}
unsigned int getTHRESHOLD_FRONT(void){
    return array_sensor[FRONT_RIGHT_SENSOR].threshold;
}
void setTHRESHOLD_DIAGONAL_RIGHT(unsigned int value){
    array_sensor[DIAGONAL_RIGHT_SENSOR].threshold = value;
}
unsigned int getTHRESHOLD_DIAGONAL_RIGHT(void){
    return array_sensor[DIAGONAL_RIGHT_SENSOR].threshold;
}
void setTHRESHOLD_DIAGONAL_LEFT(unsigned int value){
    array_sensor[DIAGONAL_LEFT_SENSOR].threshold = value;
}
unsigned int getTHRESHOLD_DIAGONAL_LEFT(void){
    return array_sensor[DIAGONAL_LEFT_SENSOR].threshold;
}
void setTHRESHOLD_RIGHT(unsigned int value){
    array_sensor[RIGHT_SENSOR].threshold = value;
}
unsigned int getTHRESHOLD_RIGHT(void){
    return array_sensor[RIGHT_SENSOR].threshold;
}
void setTHRESHOLD_LEFT(unsigned int value){
    array_sensor[LEFT_SENSOR].threshold = value;
}
unsigned int getTHRESHOLD_LEFT(void){
    return array_sensor[LEFT_SENSOR].threshold;
}
void setNUMBER_SAMPLES(unsigned int value){
    const_NUMBER_SAMPLES = value;
}
unsigned int getNUMBER_SAMPLES(void){
    return const_NUMBER_SAMPLES;
}
// END OF DELETING

void sensor_setup(){
    array_sensor[FRONT_RIGHT_SENSOR].channel = 0b0000000000000010;
    array_sensor[FRONT_RIGHT_SENSOR].value = 0;
    array_sensor[FRONT_RIGHT_SENSOR].threshold = 200;

    array_sensor[FRONT_LEFT_SENSOR].channel = 0b0000000100000000;
    array_sensor[FRONT_LEFT_SENSOR].value = 0;
    array_sensor[FRONT_LEFT_SENSOR].threshold = 200;

    array_sensor[DIAGONAL_RIGHT_SENSOR].channel = 0b0000000000000100;
    array_sensor[DIAGONAL_RIGHT_SENSOR].value = 0;
    array_sensor[DIAGONAL_RIGHT_SENSOR].threshold = 100;

    array_sensor[DIAGONAL_LEFT_SENSOR].channel = 0b0000000010000000;
    array_sensor[DIAGONAL_LEFT_SENSOR].value = 0;
    array_sensor[DIAGONAL_LEFT_SENSOR].threshold = 50;

    array_sensor[RIGHT_SENSOR].channel = 0b0000000000001000;
    array_sensor[RIGHT_SENSOR].value = 0;
    array_sensor[RIGHT_SENSOR].threshold = 150;//100
    array_side_sensor[RIGHT_SENSOR].number_samples = 0;

    array_sensor[LEFT_SENSOR].channel = 0b0000000001000000;
    array_sensor[LEFT_SENSOR].value = 0;
    array_sensor[LEFT_SENSOR].threshold = 200; //100
    array_side_sensor[LEFT_SENSOR].number_samples = 0;
}

void Sample(unsigned char S1){
    ADCON1bits.ADON=0;
    ADCSSL=(array_sensor[S1].channel);
    ADCON1bits.ADON=1;
    resetFlagInterrupt();
    ADCON1bits.ASAM=1; //stop the sampling
    while(!getFlagInterrupt());
    ADCON1bits.ASAM=0; //stop the sampling
    array_sensor[S1].value = ADCBUF0;
}

void setSideSensorValue(unsigned char S1, unsigned int value){
    unsigned char i;
    if (array_side_sensor[S1].number_samples < const_NUMBER_SAMPLES)
        array_side_sensor[S1].number_samples ++;
    for (i=(array_side_sensor[S1].number_samples-1);i>0;i--)
        array_side_sensor[S1].values[i]=array_side_sensor[S1].values[i-1];
    array_side_sensor[S1].values[0] = value;
}

void resetNumberSamples(void){
    array_side_sensor[LEFT_SENSOR].number_samples = 0;
    array_side_sensor[RIGHT_SENSOR].number_samples = 0;
}

unsigned int getSideSensorValue(unsigned char S1){
    unsigned char i;
    unsigned int value = 0;
    for (i=0;i<array_side_sensor[S1].number_samples;i++)
        value=value+array_side_sensor[S1].values[i];
    value=(unsigned int) value/array_side_sensor[S1].number_samples;
    return value;
}

void WaitSample(unsigned char S1){
    while(array_side_sensor[S1].number_samples == 0);
}

unsigned int getSensorValue(unsigned char S1){
    return array_sensor[S1].value;
}

unsigned char IsThereWallBySensor(unsigned char sensor){
    if ((sensor == FRONT_LEFT_SENSOR)||(sensor == FRONT_RIGHT_SENSOR))
        return (((getSensorValue(FRONT_LEFT_SENSOR) + getSensorValue(FRONT_RIGHT_SENSOR))/2) > array_sensor[FRONT_RIGHT_SENSOR].threshold);
    else
        return (getSensorValue(sensor) > array_sensor[sensor].threshold);
}

unsigned char IsThereWall(unsigned char direction){
    if (getCurrentDirection() == direction) return IsThereWallBySensor(FRONT_LEFT_SENSOR);
    else if (TurnRightOrLeft(getCurrentDirection(), direction) == RIGHT) return IsThereWallBySensor(RIGHT_SENSOR);
    else return IsThereWallBySensor(LEFT_SENSOR);
 }

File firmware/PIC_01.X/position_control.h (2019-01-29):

/* 
 * File:   position_control.h
 * Author: TúlioDapper
 *
 * Created on 28 January 2015, 22:14
 */

#ifndef POSITION_CONTROL_H
#define	POSITION_CONTROL_H

#define DISTANCE_FOWARD 2800
#define DISTANCE_FOWARD_MID_CELL_OUT 1400
#define DISTANCE_FOWARD_MID_CELL_IN 1800
#define DISTANCE_FOWARD_STOP_WALL 500
#define DISTANCE_TURN 1050
#define REFERENCE_VELOCITY_FOWARD 15
#define REFERENCE_VELOCITY_TURN 10
#define REFERENCE_VELOCITY_FOWARD_FAST 15
#define REFERENCE_VELOCITY_TURN_FAST 10
#define CONSTANT_CORRECTION_VELOCITY 0.06 // = (10/512)

#define WEST 0
#define NORTH 1
#define EAST 2
#define SOUTH 3

#define LEFT 0
#define RIGHT 1

#define STATE_STOPPED 0 // = (10/512)
#define STATE_MOVING_FORWARD 1 // = (10/512)
#define STATE_MOVING_TURN 2 // = (10/512)

void addPosition(int value);
void UpdatePosition(char trigger);
unsigned int getReferenceVelocityFoward(void);
unsigned int getReferenceVelocityTurn(void);
float getConstCorrectionVelocity(void);
unsigned int getFlagStop(void);
void Move(unsigned int desired_direction, unsigned int cells, unsigned char fast);
int getCurrentDirection(void);
unsigned int TurnRightOrLeft(unsigned int current_direction, unsigned int desired_direction);
unsigned int InvertDirection(unsigned int direction);
unsigned int NextDirection(unsigned int current_direction, unsigned int right_left);
void ChangeDirection(unsigned int direction);
void ResetParameters(void);

// START OF DELETING
void setDISTANCE_FOWARD(unsigned int value);
void setDISTANCE_FOWARD_MID_CELL_IN(unsigned int value);
void setDISTANCE_FOWARD_MID_CELL_OUT(unsigned int value);
void setDISTANCE_FOWARD_STOP_WALL(unsigned int value);
void setDISTANCE_TURN(unsigned int value);
void setREFERENCE_VELOCITY_FOWARD(unsigned int value);
void setREFERENCE_VELOCITY_TURN(unsigned int value);
void setCONSTANT_CORRECTION_VELOCITY(unsigned int value);
void setCONSTANT_CORRECTION_VELOCITY_DIVISOR(unsigned int value);
void setREFERENCE_VELOCITY_FOWARD_FAST(unsigned int value);
void setREFERENCE_VELOCITY_TURN_FAST(unsigned int value);
// END OF DELETING

#endif	/* POSITION_CONTROL_H */
